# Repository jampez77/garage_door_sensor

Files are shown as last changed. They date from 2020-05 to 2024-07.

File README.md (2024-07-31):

# Home Assistant Sommer Pro+ / Base+ Garage Door Opener

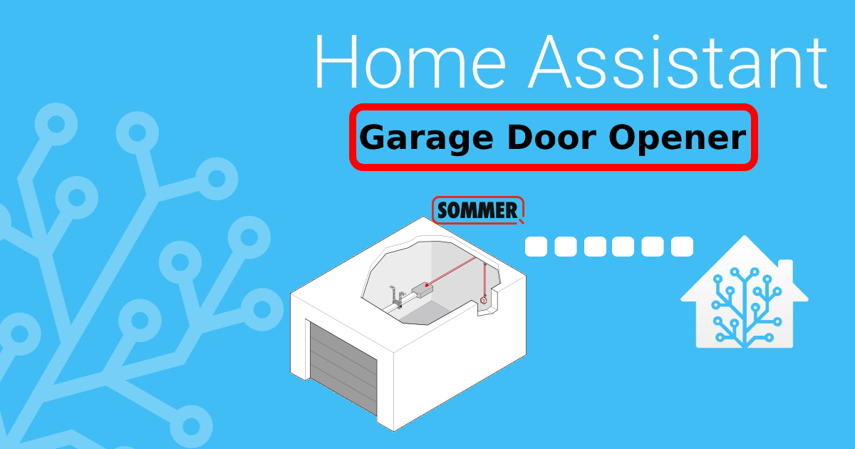
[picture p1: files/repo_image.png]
Home Assistant Sommer Pro+ / Base+ Garage Door Opener


This is my version of the excellent [garage_pi](https://github.com/azrael783/garage_pi) project by [Daniel](https://github.com/azrael783/) that uses a WeMos D1 mini instead of a Raspberry Pi Zero.

Enjoying this? Help me out with a :beers: or :coffee:!

coffee (https://www.buymeacoffee.com/whenitworks)

## Prerequisites ##

**Software**
* [Arduino IDE](https://www.arduino.cc/en/main/software) - I'm using v1.8.12
* Arduino JSON - v6.15.1
* PubSubClient - v2.7.0
* ESP8266WiFi
* ArduinoOTA

**Hardware**

* [Sommer Pro+ / Base+](https://www.sommer.eu/en-GB/pro-base.html)
* [Sommer Conex Adapter](https://www.sommer-shops.eu/de/conex.html)
* [Sommer Output OC Adapter](https://www.amazon.co.uk/gp/product/B07XZKDFX9/ref=ppx_yo_dt_b_asin_title_o05_s00?ie=UTF8&psc=1)
* [Wemos D1 Mini](https://docs.wemos.cc/en/latest/d1/d1_mini.html)
* [1 Channel Relay Shield](https://www.amazon.co.uk/gp/product/B07DK1FZF9/ref=ppx_yo_dt_b_asin_title_o03_s00?ie=UTF8&psc=1)
* [A 24V to 12v USB Power Adaptor](https://www.amazon.co.uk/gp/product/B07NMPDDN7/ref=ppx_yo_dt_b_asin_title_o02_s00?ie=UTF8&psc=1)
* [Wemos D1 Mini Relay Case](https://www.thingiverse.com/thing:2667568)

## Setup ##

**Flashing project to the WeMos**

Once you have setup your software, you first need to download this project, by clicking `clone -> Download ZIP`.

Unzip the file and navigate to the contents. you should see a file named `My_Helper_sample.h`, go ahead and rename it to `My_Helper.h`.

Now open `garage_door_sensor.ino`. Doing so should open it in the [Arduino IDE](https://www.arduino.cc/en/main/software).

You do not need to make any changes to the `garage_door_sensor` script itself!

Click on the `My_Helper.h` tab, that is where you will add your WiFi credentials for your home network & your MQTT details.

**Wiring**

You will need to solder a wire to `G` and `A0` on the bottom of the D1 Mini. Plug these into the `GND` and `OUT` pins on the Output OC PCB respectively.

Connect the relay to the Sommer Conex PCB. The `NO` terminal should connect to `T1` on the Conex, `NC` to `T2`, with `COM` terminal connecting to the centre pin.

Finally the USB power Adapter needs to be plugged into the `24v` and `Ground` of the Sommer circuit board.

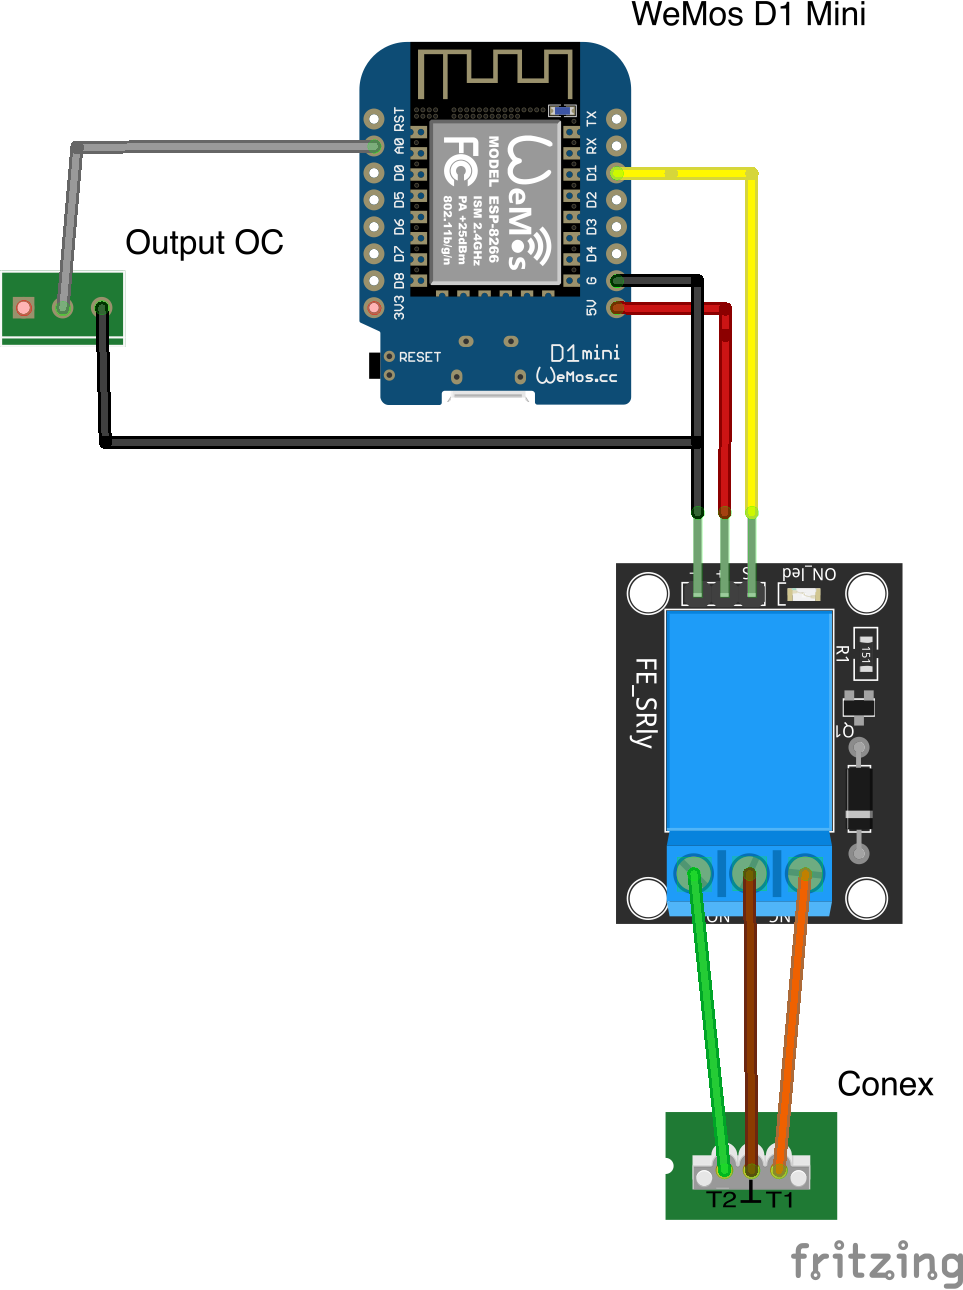
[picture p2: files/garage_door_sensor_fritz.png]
Home Assistant Sommer Conex wiring diagram


## Upload ##

The next step, once you're happy with the details is to upload the project to the Wemos D1 Mini.

To do that you select `Tools` from the top menu within the IDE.

Then you need to set the upload parameters to the following;

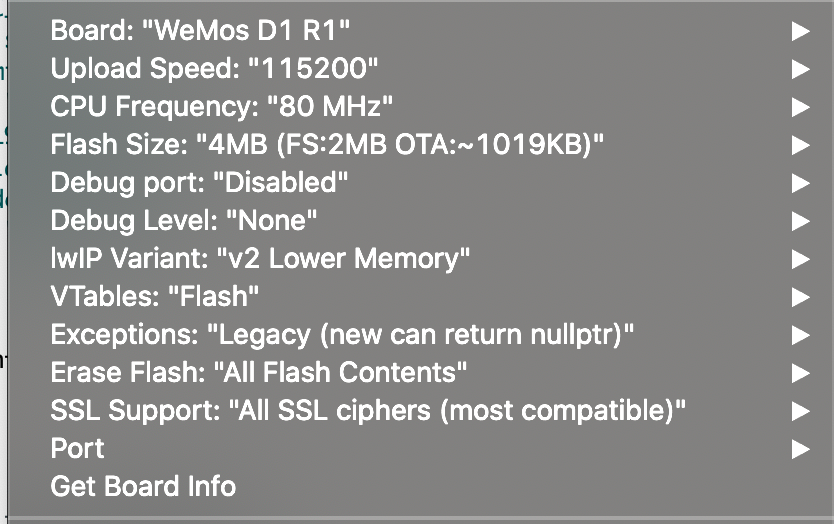
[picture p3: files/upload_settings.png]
Arduino IDE Upload settings


The next step is to simply plug your device in the computer, Go to `Tools -> Port` and select it.

For me this usually says something `dev/usbserial...`

You will only need the device plugged in on your first upload, after that you should see your devices name and it's IP address in the port list.

Now you just click on the upload button in the top left corner of the IDE, it's the right-facing arrow.

After a bit of time compiling, the script should be uploaded to the device and begin scanning for the car.

You can see what the device is doing by going to `Tools -> Serial Monitor`

If the upload doesn't work the most likely cause is that you forgot to rename the `My_Helper_sample.h` file or import the above libraries.

## Integrating with Home Assistant ##

The simplest way to integrate with [Home Assistant](https://home-assistant.io) is to turn on [MQTT discovery](https://www.home-assistant.io/docs/mqtt/discovery/). With this activated the device will be added automatically.

Alternatively you can add a new `cover` to the `configuration.yaml` like this:

    cover:
    - platform: mqtt
      name: Garage Door
      command_topic: "homeassistant/cover/garage/set"
      state_topic: "homeassistant/cover/garage/state"
      state_open: "open"
      state_opening: "opening"
      state_closed: "closed"
      state_closing: "closing"
      payload_open: "OPEN"
      payload_close: "CLOSE"
      qos: 1
      optimistic: true
      device_class: garage

## Finshed Product ##

Here is what the final project looks like for me now:

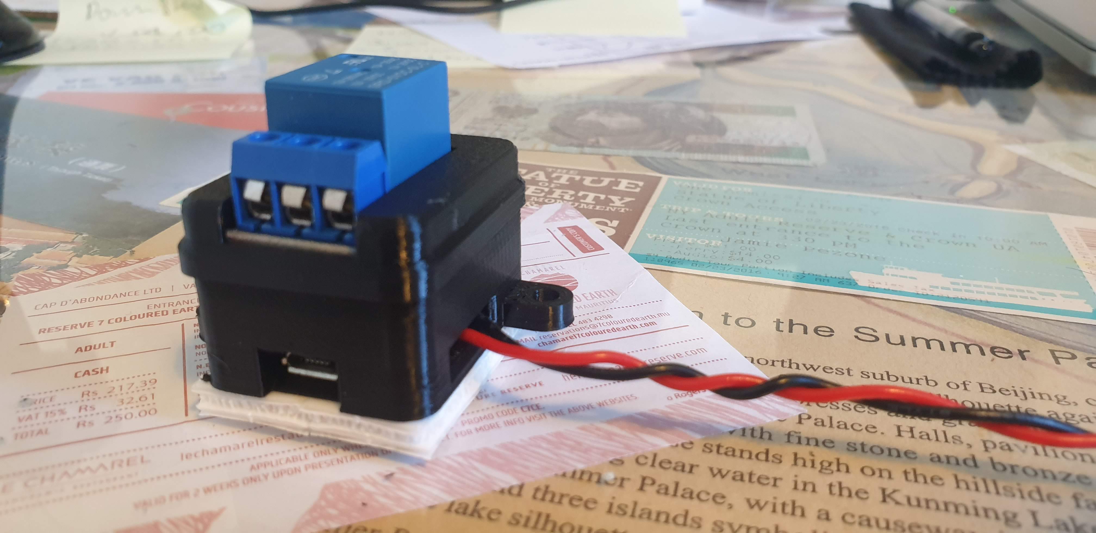
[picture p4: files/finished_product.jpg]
Finished Product

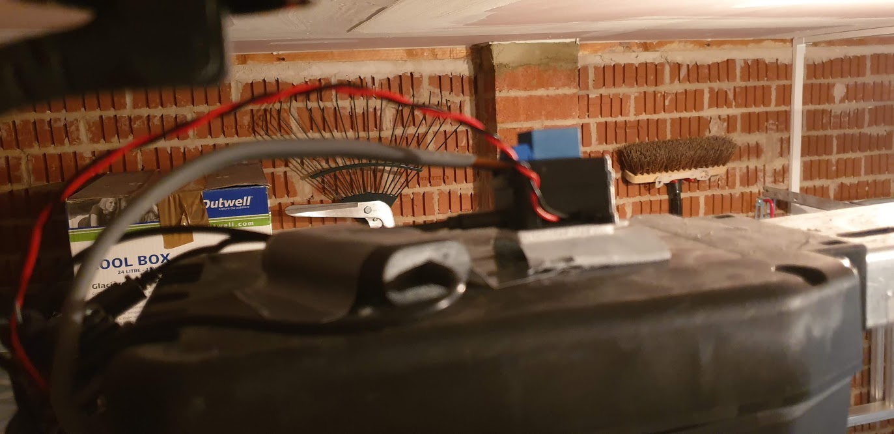
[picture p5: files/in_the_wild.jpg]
In the Wild


## Changelog ##

### Version 1.3 - Bug fixes ###

Added an additional check for the door status to prevent incorrect status being sent.

State is now checked twice with a gap of 0.5 seconds. MQTT publish is only done when both values agree on a state and that state is different from the previous one.

### Version 1.2 - Added LED status indicator and WiFi auto reconnect. ###

* Solid light = No WiFi connection
* Flashing Light = no MQTT connection
* No light = connection established

WiFi will now attempt to reconnect to network if it loose it post setup.

### Version 1.1 - Better integration with Home Assistant. ###

Added Device Registry info fo better integration with Home Assistants UI.

Make, Model, Version etc.

Should appear as a device with one entity upon initial connection.

### Version 1.0 - Better integration with Home Assistant, Over The Air updates ###

Moved to a 1 Channel Relay model.

Added analog input for Output OC to receive live door status.

ArduinoOTA for wireless code updates.

Added MQTT config on boot to integrate seamlessly with Home Assistant.

Added availability topic so we can report an offline/unavailable status to Home Assistant.

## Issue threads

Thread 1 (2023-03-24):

Old project code

KobeNuyts, 2023-03-24:
Hello, I found [this](https://arduino.stackexchange.com/questions/75704/what-are-the-best-gpio-pins-to-use-for-my-project) project online, and it's exactly what I need, but I can only find the new code with the [Output OC Adapter](https://www.amazon.co.uk/gp/product/B07XZKDFX9/ref=ppx_yo_dt_b_asin_title_o05_s00?ie=UTF8&psc=1), but I can't buy it where I live and sending it will get quite expensive.
So I waned to ask if u still got the old code with the 2 switches. And if you could maybe send it to me?
Thanks in advance and kind Regards Kobe

(Here is a picture by what I mean)
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

KobeNuyts, 2023-04-07:
Thanks for the help I'll try the code

Closed 2023-04-14.

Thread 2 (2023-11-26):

Revised version without need of the conex adapter

bvbruwae, 2023-11-26:
Hi,
Thanks for this great project. I was looking for a cheap DIY way to connect my garage door and this seems to be the perfect solution. I did however tried a slight modification that cuts out the need for the Sommer Conex adapter as that adapter was very expensive and I believe it should be possible to trigger the garagedoor without the adapter. By connecting the two connection terminals at the top left of the Sommer PCB (see attached image) with a little copper wire, I was able to give my garagedoor a signal to either start opening when the door is closed or close when the door is open.
So by connecting the relay to those existing connection terminals instead of to the conex adapter I thought I could achieve the same result. However, the solution doesn't seem to work yet. I can see the UI appear in HomeAssistant and when i click the buttons I can hear the relay clicking, however that doesn't open the gate. But when I connect both terminals with a copper wire for about a second it does start opening the gate. I don't really understand why the relay does not achieve the same result. Maybe the relay doesn't close for long enough? Is there any way to tell the relay to stay closed for about a second or more when clicking the buttons in HA?

I'm very new to the whole process and arduino, so any help would be appreciated.
Is there a benefit in using the conex adpater instead of simply using the existing connection terminals?
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

Something else I've noticed is that the gate status (open/closed) coming from the output OC (?) doesn't always update very quickly. But I can live with that as long as I can at least get the gate to open :)

b0rv3g4r4, 2024-05-31:
I think thats ur problem is the "pulse" effect.
Are you leaving the relay active? or activating it and deactivating it after 1 second?

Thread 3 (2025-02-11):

Home Assistant door state float

dannypar, 2025-02-11:
Hello! First of, thank you for your great work.

I am facing an issue, after implementing your solution with my Sommer garage door. The state value of door sensor in Home Assistant is changing constantly, like every few seconds, from opened to closed. Garage door is working as intended, no problem with that. Whole thing connected with Sommer controller using ~1,5m cables (could be an issue?) and added by MQTT autodiscovery.

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

dannypar, 2025-02-12:
Thank you for your reply!

sadly, i'm not that good with mqtt packets so will need some more accurate instructions- i need to send those increment/decrement payloads on some specific device topic, like: homeassistant/cover/garage/door/state ?

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

dannypar, 2025-02-13:
Ok, i guess i figured it out, got a constant "closed" state since 15 minutes by debug topic and some trial and error.

Thank you!

Closed 2025-02-13.

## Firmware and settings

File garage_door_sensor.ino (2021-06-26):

#include <ESP8266WiFi.h>
#include <PubSubClient.h>
#include <ArduinoJson.h>
#include <ArduinoOTA.h>
#include "My_Helper.h"

//ALL CONFIG CHANGES ARE LOCATED IN My_Helper.h//
//ALL CONFIG CHANGES ARE LOCATED IN My_Helper.h//
//ALL CONFIG CHANGES ARE LOCATED IN My_Helper.h//
//ALL CONFIG CHANGES ARE LOCATED IN My_Helper.h//
//ALL CONFIG CHANGES ARE LOCATED IN My_Helper.h//
//ALL CONFIG CHANGES ARE LOCATED IN My_Helper.h//
//ALL CONFIG CHANGES ARE LOCATED IN My_Helper.h//
//ALL CONFIG CHANGES ARE LOCATED IN My_Helper.h//
//ALL CONFIG CHANGES ARE LOCATED IN My_Helper.h//

WiFiClient espClient;
PubSubClient client(espClient);

void setup() {

  pinMode(relaySwitch, OUTPUT);
  pinMode(ledPin, OUTPUT);
  pinMode(doorInput, INPUT);
  
  Serial.begin(115200);
 
  setup_wifi();
  client.setServer(mqtt_server, 1883);
  client.setCallback(callback);
  client.setBufferSize(1024);

  while(!configDetailsSent){
     if (connectClient()) {
       
      sendConfigDetailsToHA();
      //send initial door status without triggering relay
      getAndSendDoorStatus();
    }
  }

  //Setup OTA
  {

    //Authentication to avoid unauthorized updates
    //ArduinoOTA.setPassword((const char *)"nidayand");

    ArduinoOTA.setHostname((mqttDeviceClientId + "-" + String(ESP.getChipId())).c_str());

    ArduinoOTA.onStart([]() {
      Serial.println("Start");
    });
    ArduinoOTA.onEnd([]() {
      Serial.println("\nEnd");
    });
    ArduinoOTA.onProgress([](unsigned int progress, unsigned int total) {
      Serial.printf("Progress: %u%%\r", (progress / (total / 100)));
    });
    ArduinoOTA.onError([](ota_error_t error) {
      Serial.printf("Error[%u]: ", error);
      if (error == OTA_AUTH_ERROR) Serial.println("Auth Failed");
      else if (error == OTA_BEGIN_ERROR) Serial.println("Begin Failed");
      else if (error == OTA_CONNECT_ERROR) Serial.println("Connect Failed");
      else if (error == OTA_RECEIVE_ERROR) Serial.println("Receive Failed");
      else if (error == OTA_END_ERROR) Serial.println("End Failed");
    });
    ArduinoOTA.begin();
  }
}

void loop() {

  //OTA client code
  ArduinoOTA.handle();

  //attempt connection to WiFi if we don't have it
  if(!espClient.connected()){
    setup_wifi();
  }

  //while connected we send the current door status
  //and trigger relay if we need to
  if(client.connected()){
    client.loop();
    delay(1000);
    digitalWrite(ledPin, HIGH);
    getAndSendDoorStatus();
  } else {
    connectClient();
  }
}

void setup_wifi() {

  delay(10);
  // We start by connecting to a WiFi network
  Serial.println();
  Serial.print("Connecting to ");
  Serial.println(ssid);

  //Set WiFi mode so we don't create an access point.
  WiFi.mode(WIFI_STA);
  WiFi.begin(ssid, password);
  
  Serial.println(WiFi.mode(WIFI_STA));
  
  while (WiFi.status() != WL_CONNECTED) {
    delay(500);
    Serial.print(".");
    digitalWrite(ledPin, LOW);
  }
  
  randomSeed(micros());
  digitalWrite(ledPin, HIGH);
  
  Serial.println("");
  Serial.println("WiFi connected");
  Serial.println("IP address: ");
  Serial.println(WiFi.localIP());
}

boolean connectClient() {
  // Loop until we're connected
  while (!client.connected()) {
    configDetailsSent = false;
    digitalWrite(ledPin, HIGH);
    delay(100);
    digitalWrite(ledPin, LOW);
    Serial.print("Attempting MQTT connection...");
    // Check connection
    if (client.connect(mqttDeviceClientId.c_str(), mqtt_user, mqtt_password, availabilityTopic, 0, true, payloadNotAvailable)) {
      // Make an announcement when connected
      Serial.println("connected");
      client.publish(availabilityTopic, payloadAvailable, true);  
      
      client.subscribe(commandTopic);
      client.subscribe(availabilityTopic);
      
      Serial.println("Subscribed to: ");
      Serial.println(commandTopic);
      Serial.println(availabilityTopic);

      while(!configDetailsSent){
        sendConfigDetailsToHA();
      }
      return true;
    } else {
      Serial.print("failed, rc=");
      Serial.print(client.state());
      Serial.println(" try again in 5 seconds");
      // Wait 5 seconds before retrying
      delay(5000);
      return false;
    }
  }
  return true;
}

void callback(char* topic, byte* message, unsigned int length) {

  String messageStr;
  
  for (int i = 0; i < length; i++) {
    messageStr += (char)message[i];
  }
  
  if (String(topic) == commandTopic) {
     Serial.print("Home Assistant Command: ");
     Serial.println(messageStr);

     if((messageStr == payloadOpen && doorStatus != opened) || messageStr == "forceOpen"){
        //open door is not already open or we are running a test.

        //trigger relay to open

        if(doorStatus == closed){
           closeTheDoor(); 
           delay(500);
        } 
         //change to transition state opening
        client.publish(stateTopic, opening, true); 
        openTheDoor();
     }else if((messageStr == payloadClose && doorStatus != closed) || messageStr == "forceClose"){
        //close door is not already closed or we are running a test

        //trigger relay to close
       
        if(doorStatus == opened){
           openTheDoor(); 
           delay(500);
        } 
        //change to transition state closing
        client.publish(stateTopic, closing, true); 
        closeTheDoor(); 
     }else if(messageStr == payloadStop){

        //make sure we undo the relevant switches to stop the motion based on the previous status
        if(doorStatus == opened){
          closeTheDoor();
        }else if(doorStatus == closed){
          openTheDoor();
        }
    }

    prevDoorStatus = doorStatus;

    //increase openThreshold by 1
    if(messageStr == "incrementOpenThreshold"){
      openThreshold = openThreshold + 1;
      String msg = "Set open threshold to: " + openThreshold;
      client.publish(stateTopic, msg.c_str(), true); 
    }

    //decrease openThreshold by 1
    if(messageStr == "decrementOpenThreshold"){
      openThreshold = openThreshold - 1;
      String msg = "Set open threshold to: " + openThreshold;
      client.publish(stateTopic, msg.c_str(), true); 
    }
  }
}

void getAndSendDoorStatus(){
   int initialDoorState = analogRead(doorInput);

   const char* initialDoorStatus = "";

   //determine initial door state based on openThreshold
  if(initialDoorState <= openThreshold){
    initialDoorStatus = opened;
  } else {
    initialDoorStatus = closed;
  }

  delay(500);

  int secondaryDoorState = analogRead(doorInput);

  //send initial and secondary readings to debug topic
  DynamicJsonDocument debugJsonDoc(100);
  debugJsonDoc["initial"] = initialDoorState;
  debugJsonDoc["secondary"] = secondaryDoorState;
  debugJsonDoc["openThreshold"] = openThreshold;

  char debugJson[100];
  serializeJsonPretty(debugJsonDoc, debugJson);
  client.publish(coverDebugTopic, debugJson, false); 

  const char* secondaryDoorStatus = "";

   //determine secondary door state based on openThreshold
  if(secondaryDoorState <= openThreshold){
    secondaryDoorStatus = opened;
  } else {
    secondaryDoorStatus = closed;
  }

  //only send new door status if initial and secondary check are in agreement
  //and if status is different from previous one
  if(initialDoorStatus == secondaryDoorStatus){
      //set door status
      if(initialDoorState <= openThreshold){
        statusToOpen();
      } else {
        statusToClosed();
      }

      sendDoorStatus();
  }
  
}

void sendDoorStatus(){
    //publish to doorStatus to HA
    //if it has changed
    //then trigger the relay if we need to
   
    if(prevDoorStatus != doorStatus){
      Serial.print("Door ");
      Serial.println(doorStatus);
      client.publish(stateTopic, doorStatus, true); 
  
      prevDoorStatus = doorStatus;
    } 
}

void closeTheDoor(){
  digitalWrite(relaySwitch, closeDoor);
}

void statusToClosed(){
  doorStatus = closed;
}

void openTheDoor(){
  digitalWrite(relaySwitch, openDoor);
}

void statusToOpen(){
  doorStatus = opened;  
}

void sendConfigDetailsToHA(){
  //Send cover entity details to home assistant on initial connection
    //for auto discovery
    StaticJsonDocument<1024> mqttConfig;
    mqttConfig["name"] = mqttDeviceName;
    mqttConfig["dev_cla"] = mqttDeviceClass; 
    mqttConfig["stat_t"] = stateTopic;
    mqttConfig["cmd_t"] = commandTopic; 
    mqttConfig["stat_open"] = opened;
    mqttConfig["stat_clsd"] = closed;
    mqttConfig["stat_closing"] = closing;
    mqttConfig["stat_opening"] = opening;
    mqttConfig["pl_open"] = payloadOpen;
    mqttConfig["pl_cls"] = payloadClose;
    mqttConfig["pl_stop"] = payloadStop;
    mqttConfig["opt"] = false;
    mqttConfig["ret"] = true;
    mqttConfig["avty_t"] = availabilityTopic;
    mqttConfig["pl_avail"] = payloadAvailable;
    mqttConfig["pl_not_avail"] = payloadNotAvailable;
    mqttConfig["uniq_id"] = mqttDeviceClientId;
    
    mqttConfig["dev"]["name"] = mqttDeviceClientId;
    mqttConfig["dev"]["mf"] = manufacturer;
    mqttConfig["dev"]["mdl"] = model;
    mqttConfig["dev"]["sw"] = softwareVersion;
    mqttConfig["dev"]["ids"][0] = mqttDeviceClientId;
    
    char json[1024];
    serializeJsonPretty(mqttConfig, json);
    client.publish(configTopic, json, true);
    configDetailsSent = true;
}

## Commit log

2020-05-23 Initial Release
    [garage_door_sensor.fzz]
2020-09-30 Upgrade / Overhaul
    Move to a 1 Channel Relay model.
    Added analog input for Output OC to recieve live door status.
    ArduinoOTA for wireless code updates.
    Added MQTT config on boot to integrate seemlessly with Home Assistant.
    Added availability topic so we can report an `offline`/`unavailable` status to Home Assistant.
    [garage_door_sensor.fzz]
2020-09-30 Added Device Registry
    Added Device Info for MQTT integration.
2020-10-16 Added LED status indicator and WiFi auto reconnect
    * Solid light = No WiFi connection
    * Flashing Light = no MQTT connection
    * No light = connection established
    WiFi will now attempt to reconnect to network if it loose it post setup.
    [garage_door_sensor.ino]
2020-12-30 Fixed erroneous state bug
    Added an additional check for the door status to prevent incorrect status being sent.
    State is now checked twice with a gap of 0.5 seconds. MQTT publish is only done when both values agree on a state and that state is different from the previous one.
    [garage_door_sensor.ino]
